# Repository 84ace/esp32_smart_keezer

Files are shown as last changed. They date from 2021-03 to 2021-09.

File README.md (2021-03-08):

<!-- PROJECT SHIELDS -->
<!--
*** I'm using markdown "reference style" links for readability.
*** Reference links are enclosed in brackets [ ] instead of parentheses ( ).
*** See the bottom of this document for the declaration of the reference variables
*** for contributors-url, forks-url, etc. This is an optional, concise syntax you may use.
*** https://www.markdownguide.org/basic-syntax/#reference-style-links
-->
[][contributors-url]
[][forks-url]
[][stars-url]
[][issues-url]
[][license-url]
[][linkedin-url]

<!-- PROJECT LOGO -->
<br />
<p align="center">
  <a href="https://github.com/84ace/esp32_smart_keezer">
    
  </a>

  <h3 align="center">ESP32 Smart Keezer</h3>

  <p align="center">
    Monitoring the beer flow!
    <br />
    <a href="https://github.com/84ace/esp32_smart_keezer/wiki"><strong>Explore the docs »</strong></a>
    <br />
    <br />
    <a href="https://github.com/84ace/esp32_smart_keezer/tree/master/board_images">Board Images</a>
    <a href="https://github.com/84ace/esp32_smart_keezer/issues">Report Bug</a>
    <a href="https://github.com/84ace/esp32_smart_keezer/issues">Request Feature</a>
  </p>
</p>

<!-- TABLE OF CONTENTS -->
<details open="open">
  <summary>Table of Contents</summary>
  <ol>
    <li>
      <a href="#about-the-project">About The Project</a>
      <ul>
        <li><a href="#main-features">Main Features</a></li>
        <li><a href="#whats-missing">What's Missing</a></li>
      </ul>
    </li>
    <li>
      <a href="#get-the-isolator">Get the Smart Keezer Gear</a>
    </li>
    <li><a href="#roadmap">Roadmap</a></li>
    <li><a href="#contributing">Contributing</a></li>
    <li><a href="#made-with">Made with</a></li>
    <li><a href="#license">License</a></li>
    <li><a href="#contact">Contact</a></li>
    <li><a href="#acknowledgements">Acknowledgements</a></li>
  </ol>
</details>

<!-- ABOUT THE PROJECT -->
## About The Project

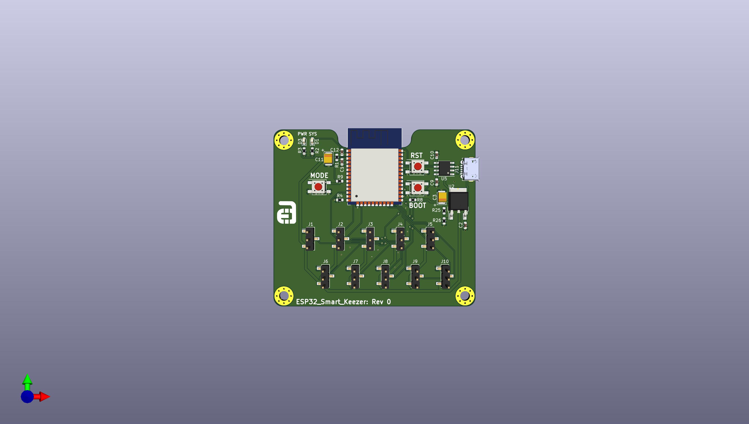
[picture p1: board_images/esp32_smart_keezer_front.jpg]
ESP32 Smart Keezer
[](https://github.com/84ace/esp32_smart_keezer/raw/master/board_images/esp32_smart_keezer_front.jpg)

The ESP32 Smart Keezer was created so that we could monitor things inside the Keezer a bit better (so we knew when we were going to run out of beer), and also so we could have a cooler way of displaying what beers were on tap.

<!-- MAIN FEATURES -->
## Main Features:
* Web based  config (webserver)
* 10 channel flow meter
* Bluetooth (to update the tap handles)
* WiFi
* USB (for power and flashing/debug)

<!-- WHAT"S MISSING -->
## What's missing:
* Many many things

If you would like to contribute an app please contact me via the <a href="https://github.com/84ace/esp32_smart_keezer/tree/master/board_images">issues</a> page.

<!-- GETTING STARTED 
## Get the hardware

There are two ways to get started: 
* You can either take the easy(er) way and buy a pre-made unit from [here](https://placeholder.com/) 
* you can send the gerber files off to your favourite fab house, order the components, assemble the board and print the enclosure yourself.

Your choice!

-->

<!-- ROADMAP -->
## Roadmap

See the [open issues](https://github.com/84ace/esp32_smart_keezer/issues) for a list of proposed features (and known issues).

<!-- CONTRIBUTING -->
## Contributing

Contributions are what make the open source community such an amazing place to be learn, inspire, and create. Any contributions you make are **greatly appreciated**.

1. Fork the Project
2. Create your Feature Branch (`git checkout -b feature/AmazingFeature`)
3. Commit your Changes (`git commit -m 'Add some AmazingFeature'`)
4. Push to the Branch (`git push origin feature/AmazingFeature`)
5. Open a Pull Request

<!-- MADE WITH -->
## Made With:
* [KiCad - Electronic Design Automation Suite](https://kicad.org/)
* [Fusion360 - CAD Software](https://www.autodesk.com.au/products/fusion-360/overview)
* [JLCPCB - PCB Fabrication Manufacturer](https://jlcpcb.com/)

<!-- LICENSE -->
## License

Distributed under the MIT License. See `LICENSE` for more information.

<!-- CONTACT -->
## Contact

84ace - [@Racea_Quigg](https://twitter.com/@RaceaQuigg)

Project Link: [https://github.com/84ace/esp32_smart_keezer](https://github.com/84ace)

<!-- MARKDOWN LINKS & IMAGES -->
<!-- https://www.markdownguide.org/basic-syntax/#reference-style-links -->
[contributors-shield]: https://img.shields.io/github/contributors/84ace/esp32_smart_keezer.svg?style=for-the-badge
[contributors-url]: https://github.com/84ace/esp32_smart_keezer/graphs/contributors
[forks-shield]: https://img.shields.io/github/forks/84ace/esp32_smart_keezer.svg?style=for-the-badge
[forks-url]: https://github.com/84ace/esp32_smart_keezer/network/members
[stars-shield]: https://img.shields.io/github/stars/84ace/esp32_smart_keezer.svg?style=for-the-badge
[stars-url]: https://github.com/84ace/esp32_smart_keezer/stargazers
[issues-shield]: https://img.shields.io/github/issues/84ace/esp32_smart_keezer.svg?style=for-the-badge
[issues-url]: https://github.com/84ace/esp32_smart_keezer/issues
[license-shield]: https://img.shields.io/github/license/84ace/esp32_smart_keezer.svg?style=for-the-badge
[license-url]: https://github.com/84ace/esp32_smart_keezer/blob/master/LICENSE.txt
[linkedin-shield]: https://img.shields.io/badge/-LinkedIn-black.svg?style=for-the-badge&logo=linkedin&colorB=555
[linkedin-url]: https://www.linkedin.com/in/acea-quigg-2007036b/
[product-screenshot]: board_images/esp32_smart_keezer_front.jpg

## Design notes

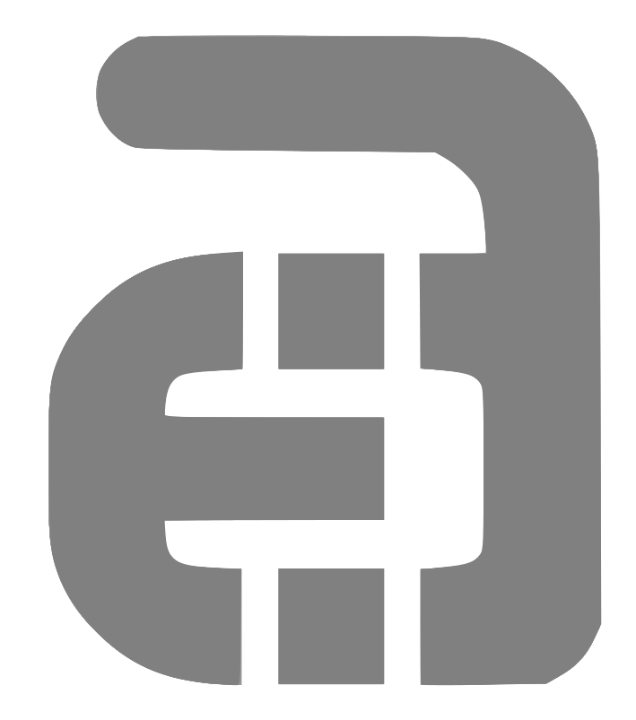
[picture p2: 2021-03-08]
images/.svg2shenzhen-cache/images/B.SilkS_g1226.png

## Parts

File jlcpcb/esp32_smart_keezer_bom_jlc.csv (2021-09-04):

Comment | Designator | Footprint | LCSC Part #
220uF | C2 | C_Elec_6.3x7.7 | C371974
220uF | C6 | CP_EIA-3528-15_AVX-H | C30242
1uF | C11 | CP_EIA-3528-21_Kemet-B | C169224
100n | C12,C1,C10,C9,C3 | C_0603_1608Metric | C14663
MAIN LED | D1 | LED_0603_1608Metric | C2286
POWER LED | D3 | LED_0603_1608Metric | C2286
SS34 | D4,D2 | D_SMA | C8678
Conn_01x03_Male | J1,J4,J5,J2,J3,J10,J8,J9,J6,J7 | PinHeader_1x03_P2.54mm_Vertical_SMD_Pin1Left | C780061
USB_B_Micro | J11 | USB_Micro_SHOU-HAN-MicroXNJ_C404969_Horizontal | C404969
Barrel_Jack_MountingPin | J12 | BarrelJack_Wuerth_6941xx301002 | C136744
47uH | L1 | L_Bourns_SRN6045TA | C36414
10k | R1,R8,R4,R9 | R_0603_1608Metric | C25804
3.6k | R2,R3 | R_0603_1608Metric | C22980
1M | R7 | R_0603_1608Metric | C22935
C492887 | SW1,SW2,SW3 | TS4550TP | C492887
ESP32-WROOM-32D | U1 | ESP32-WROOM-32 | C473012
XL1509_SOP8 | U2 | SOIC-8_3.9x4.9mm_P1.27mm | C2681226
CH340N | U5 | SOIC-8_3.9x4.9mm_P1.27mm | C506813

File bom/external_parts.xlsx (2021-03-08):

$8.82 | 3.3V 1/2" Stainless 1-30LPM | https://www.aliexpress.com/item/32834744712.html
 | 3.3V 3/4" Aluminium 1-30LPM | https://www.aliexpress.com/item/32883880511.html

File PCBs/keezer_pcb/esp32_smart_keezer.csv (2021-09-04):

Id | Designator | Package | Quantity | Designation | Supplier and ref
1 | Ref** | aces_electronics_small_front | 1 | Val**
2 | J11 | USB_Micro_SHOU-HAN-MicroXNJ_C404969_Horizontal | 1 | USB_B_Micro
3 | H1,H1,H1,H1 | MountingHole_3.2mm_M3_Pad_Via | 4 | MountingHole_3.2mm_M3_Pad_Via
4 | C1,C9,C10,C12,C3 | C_0603_1608Metric | 5 | 100n
5 | C11 | CP_EIA-3528-21_Kemet-B | 1 | 1uF
6 | D1 | LED_0603_1608Metric | 1 | MAIN LED
7 | D3 | LED_0603_1608Metric | 1 | POWER LED
8 | R1,R4,R8,R9 | R_0603_1608Metric | 4 | 10k
9 | R2,R3 | R_0603_1608Metric | 2 | 3.6k
10 | U1 | ESP32-WROOM-32 | 1 | ESP32-WROOM-32D
11 | SW1,SW2,SW3 | TS4550TP | 3 | C492887
12 | U5 | SOIC-8_3.9x4.9mm_P1.27mm | 1 | CH340N
13 | J1,J2,J3,J4,J5,J6,J7,J8,J9,J10 | PinHeader_1x03_P2.54mm_Vertical_SMD_Pin1Left | 10 | Conn_01x03_Male
14 | D4,D2 | D_SMA | 2 | SS34
15 | J12 | BarrelJack_Wuerth_6941xx301002 | 1 | Barrel_Jack_MountingPin
16 | C2 | C_Elec_6.3x7.7 | 1 | 220uF
17 | C6 | CP_EIA-3528-15_AVX-H | 1 | 220uF
18 | L1 | L_Bourns_SRN6045TA | 1 | 47uH
19 | R7 | R_0603_1608Metric | 1 | 1M
20 | U2 | SOIC-8_3.9x4.9mm_P1.27mm | 1 | XL1509_SOP8

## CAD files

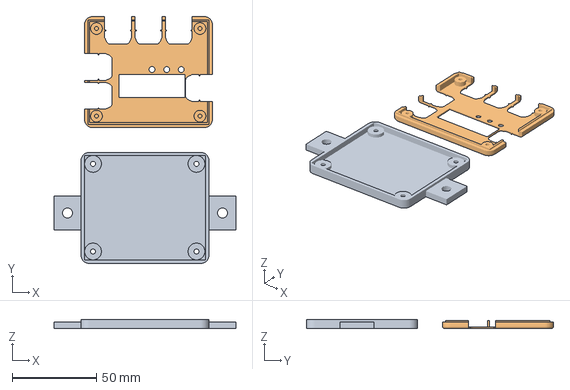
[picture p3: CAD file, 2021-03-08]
enclosure/REV_A.3mf
108.0 x 146.6 x 5.60 mm
e16b49ae-1aed-4ee6-b51c-7ca3a6dbe336.stl
ccecfdcf-7b8e-40b3-9f25-145435015e84.stl

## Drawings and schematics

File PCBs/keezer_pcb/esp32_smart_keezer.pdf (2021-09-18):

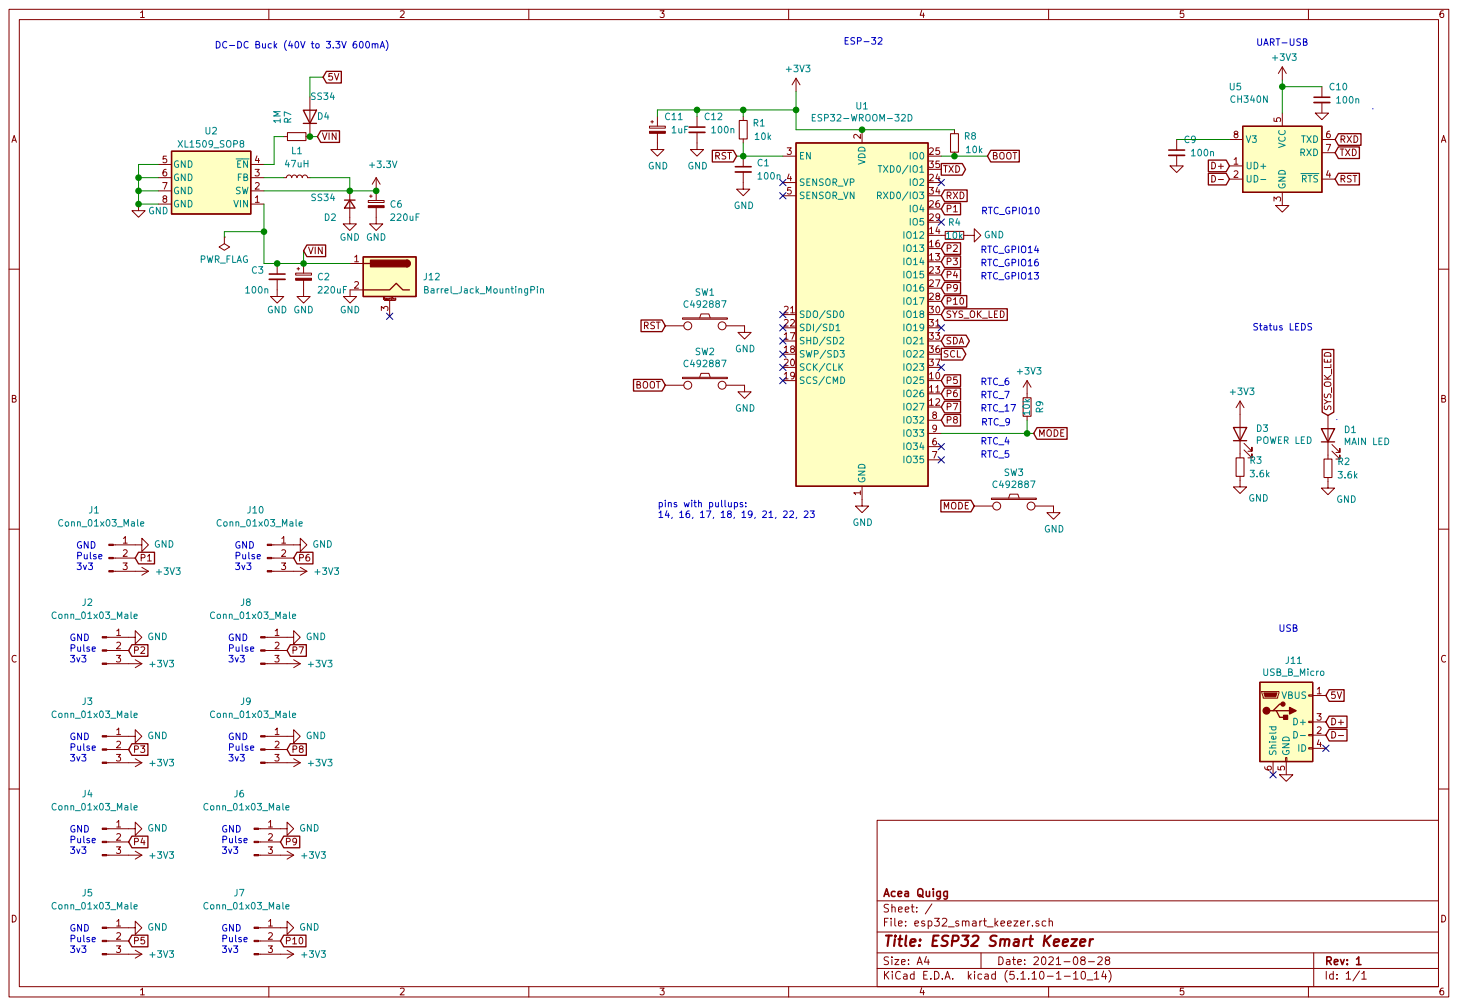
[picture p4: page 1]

File: esp32_smart_keezer.sch Sheet: / Acea Quigg

Id: 1/1 Title: ESP32 Smart Keezer

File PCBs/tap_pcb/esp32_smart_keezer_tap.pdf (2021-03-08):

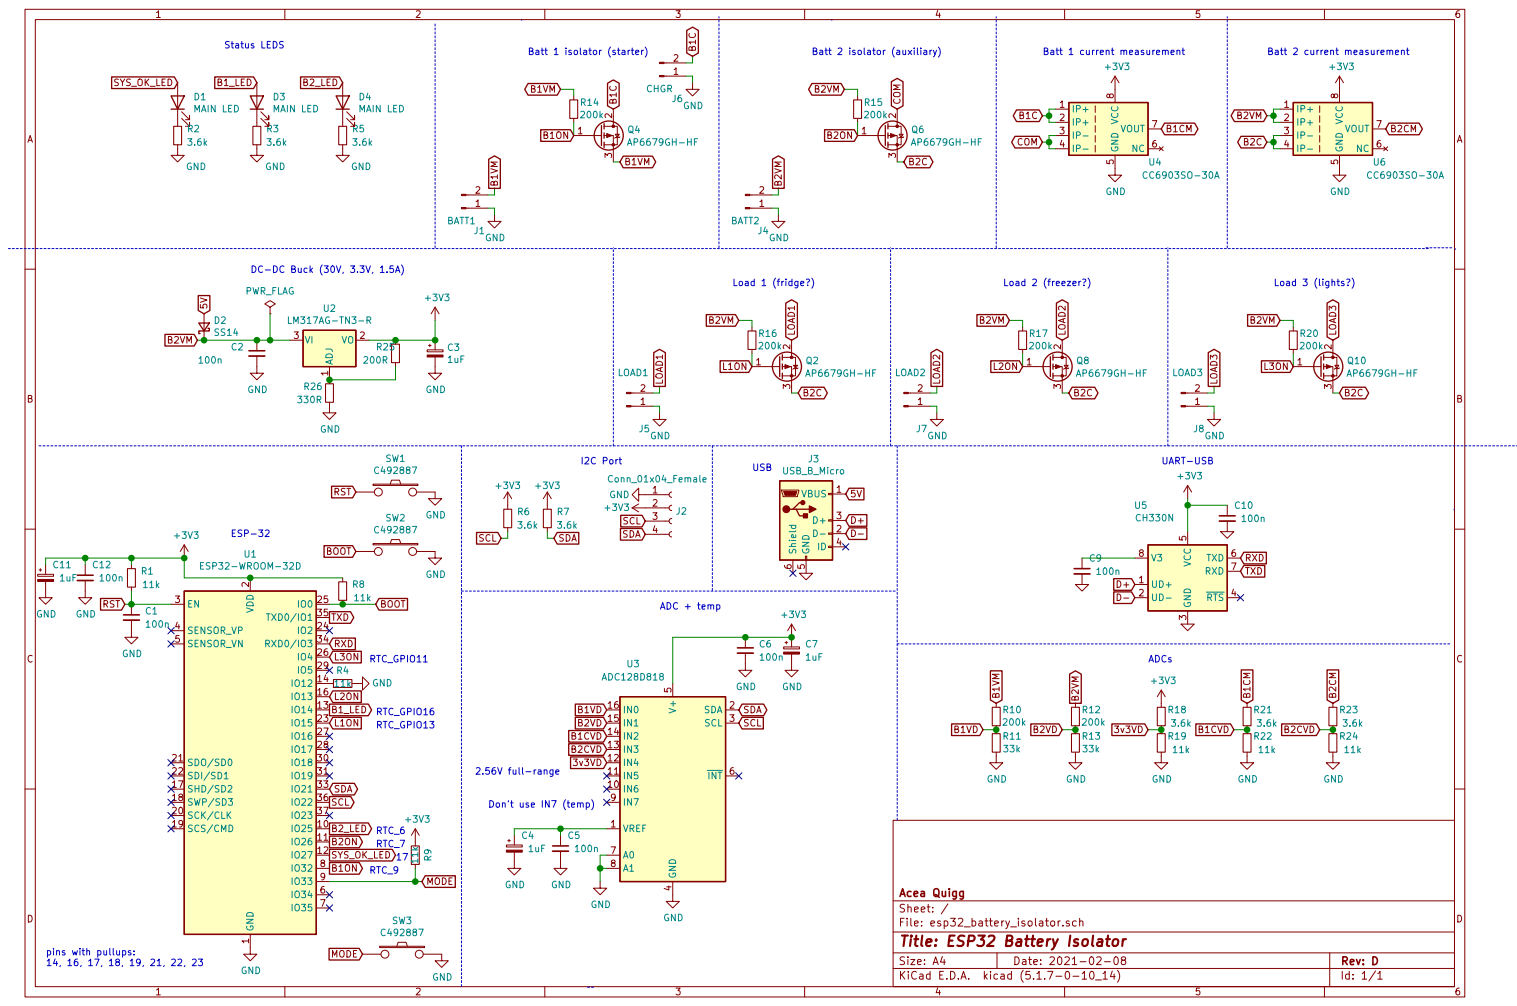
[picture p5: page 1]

Batt 2 isolator (auxiliary) Status LEDS

Load 3 (lights?) UART-USB

2 SCK/CLK 20 SDO/SD0 21 SDI/SD1 22

File: esp32_battery_isolator.sch Sheet: / Acea Quigg GND GND

Id: 1/1 Title: ESP32 Battery Isolator

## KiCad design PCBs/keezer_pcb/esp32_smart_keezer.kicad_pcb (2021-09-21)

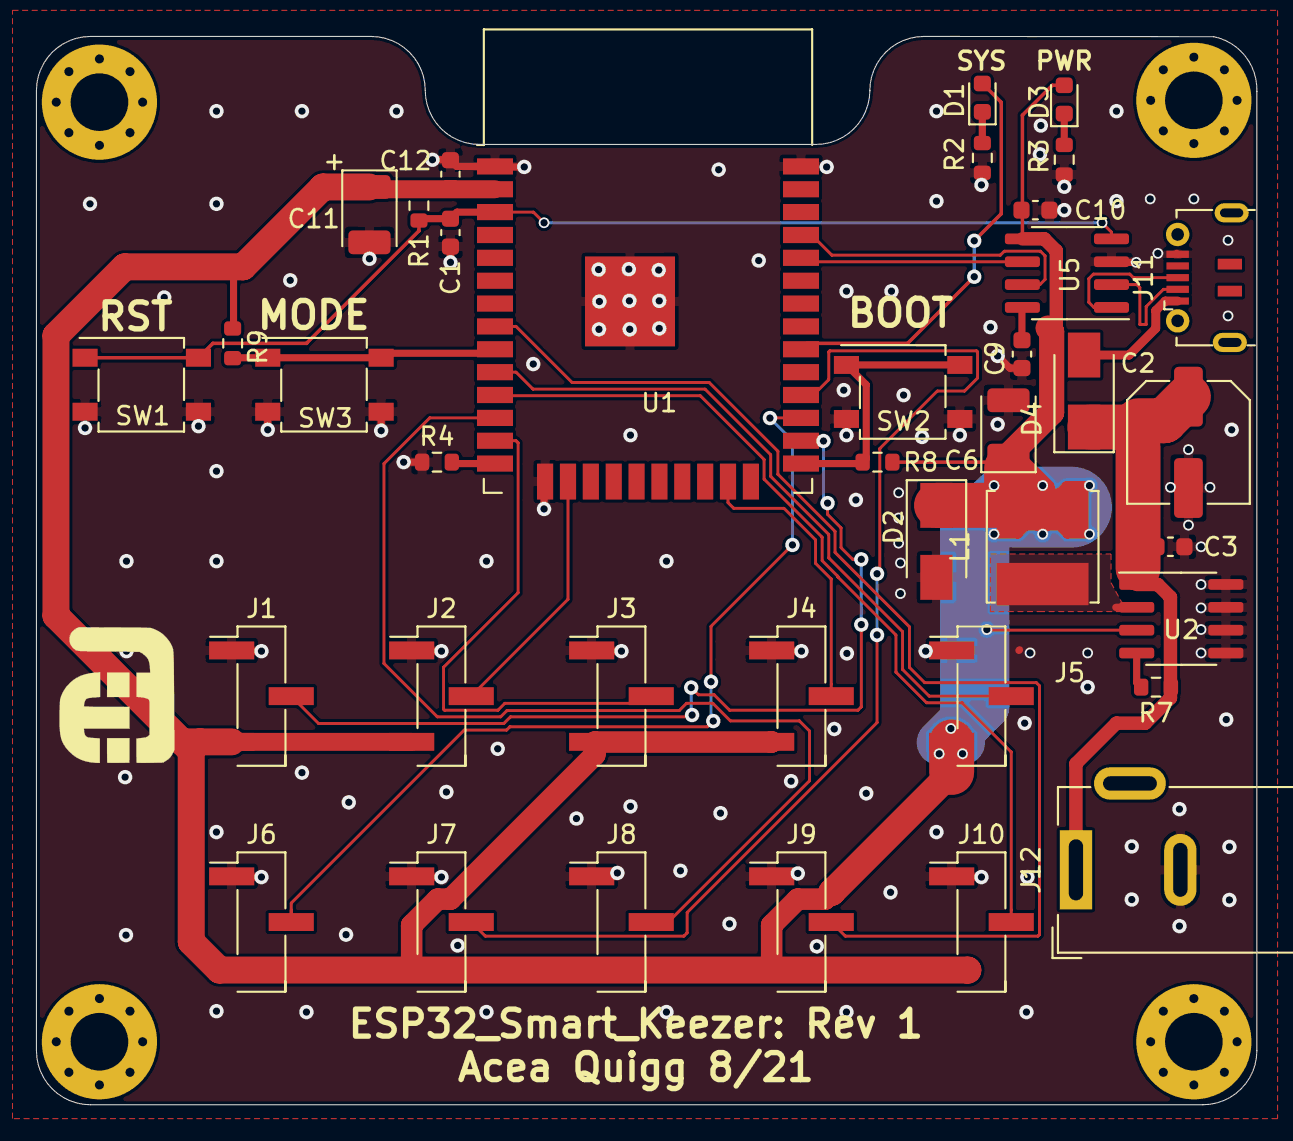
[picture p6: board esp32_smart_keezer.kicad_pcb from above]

Board: 2 copper layers, 67.8 x 59.3 mm, 43 parts (0 on the bottom side), 28 nets.

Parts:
C1, C3, C9, C10, C12: 100n; C_0603_1608Metric
C2: 220uF; C_Elec_6.3x7.7
C6: 220uF; CP_EIA-3528-15_AVX-H
C11: 1uF; CP_EIA-3528-21_Kemet-B
D1: MAIN LED; LED_0603_1608Metric
D2, D4: SS34; D_SMA
D3: POWER LED; LED_0603_1608Metric
H1, H1#2, H1#3, H1#4: MountingHole_3.2mm_M3_Pad_Via
J1, J2, J3, J4, J5, J6, J7, J8, J9, J10: Conn_01x03_Male; PinHeader_1x03_P2.54mm_Vertical_SMD_Pin1Left
J11: USB_B_Micro; USB_Micro_SHOU-HAN-MicroXNJ_C404969_Horizontal
J12: Barrel_Jack_MountingPin; BarrelJack_Wuerth_6941xx301002
L1: 47uH; L_Bourns_SRN6045TA
R1, R4, R8, R9: 10k; R_0603_1608Metric
R2, R3: 3.6k; R_0603_1608Metric
R7: 1M; R_0603_1608Metric
Ref**: Val**; aces_electronics_small_front
SW1, SW2, SW3: C492887; TS4550TP
U1: ESP32-WROOM-32D; ESP32-WROOM-32
U2: XL1509_SOP8; SOIC-8_3.9x4.9mm_P1.27mm
U5: CH340N; SOIC-8_3.9x4.9mm_P1.27mm

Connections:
5V: D4.2, J11.1
+3V3: C6.1, C10.1, C11.1, C12.1, D2.1, D3.2, J1.3, J2.3, J3.3, J4.3, J5.3, J6.3, J7.3, J8.3, J9.3, J10.3, L1.2, R1.1, R8.1, R9.2, U1.2, U2.3, U5.5
BOOT: R8.2, SW2.1, U1.25
D+: J11.3, U5.1
D-: J11.2, U5.2
GND: C1.2, C2.2, C3.2, C6.2, C9.2, C10.2, C11.2, C12.2, D2.2, J1.1, J2.1, J3.1, J4.1, J5.1, J6.1, J7.1, J8.1, J9.1, J10.1, J11.5, J12.2, R2.2, R3.2, R4.1, SW1.2, SW2.2, SW3.2, U1.1, U1.15, U1.38, U1.39, U2.5, U2.6, U2.7, U2.8, U5.3
MODE: R9.1, SW3.1, U1.9
unnamed: C9.1, U5.8
unnamed: D1.1, R2.1
unnamed: D3.1, R3.1
unnamed: L1.1, U2.2
unnamed: R4.2, U1.14
unnamed: R7.2, U2.4
P1: J1.2, U1.26
P2: J2.2, U1.16
P3: J3.2, U1.13
P4: J4.2, U1.23
P5: J5.2, U1.10
P6: J10.2, U1.11
P7: J8.2, U1.12
P8: J9.2, U1.8
P9: J6.2, U1.27
P10: J7.2, U1.28
RST: C1.1, R1.2, SW1.1, U1.3, U5.4
RXD: U1.34, U5.6
SYS_OK_LED: D1.2, U1.30
TXD: U1.35, U5.7
VIN: C2.1, C3.1, D4.1, J12.1, R7.1, U2.1

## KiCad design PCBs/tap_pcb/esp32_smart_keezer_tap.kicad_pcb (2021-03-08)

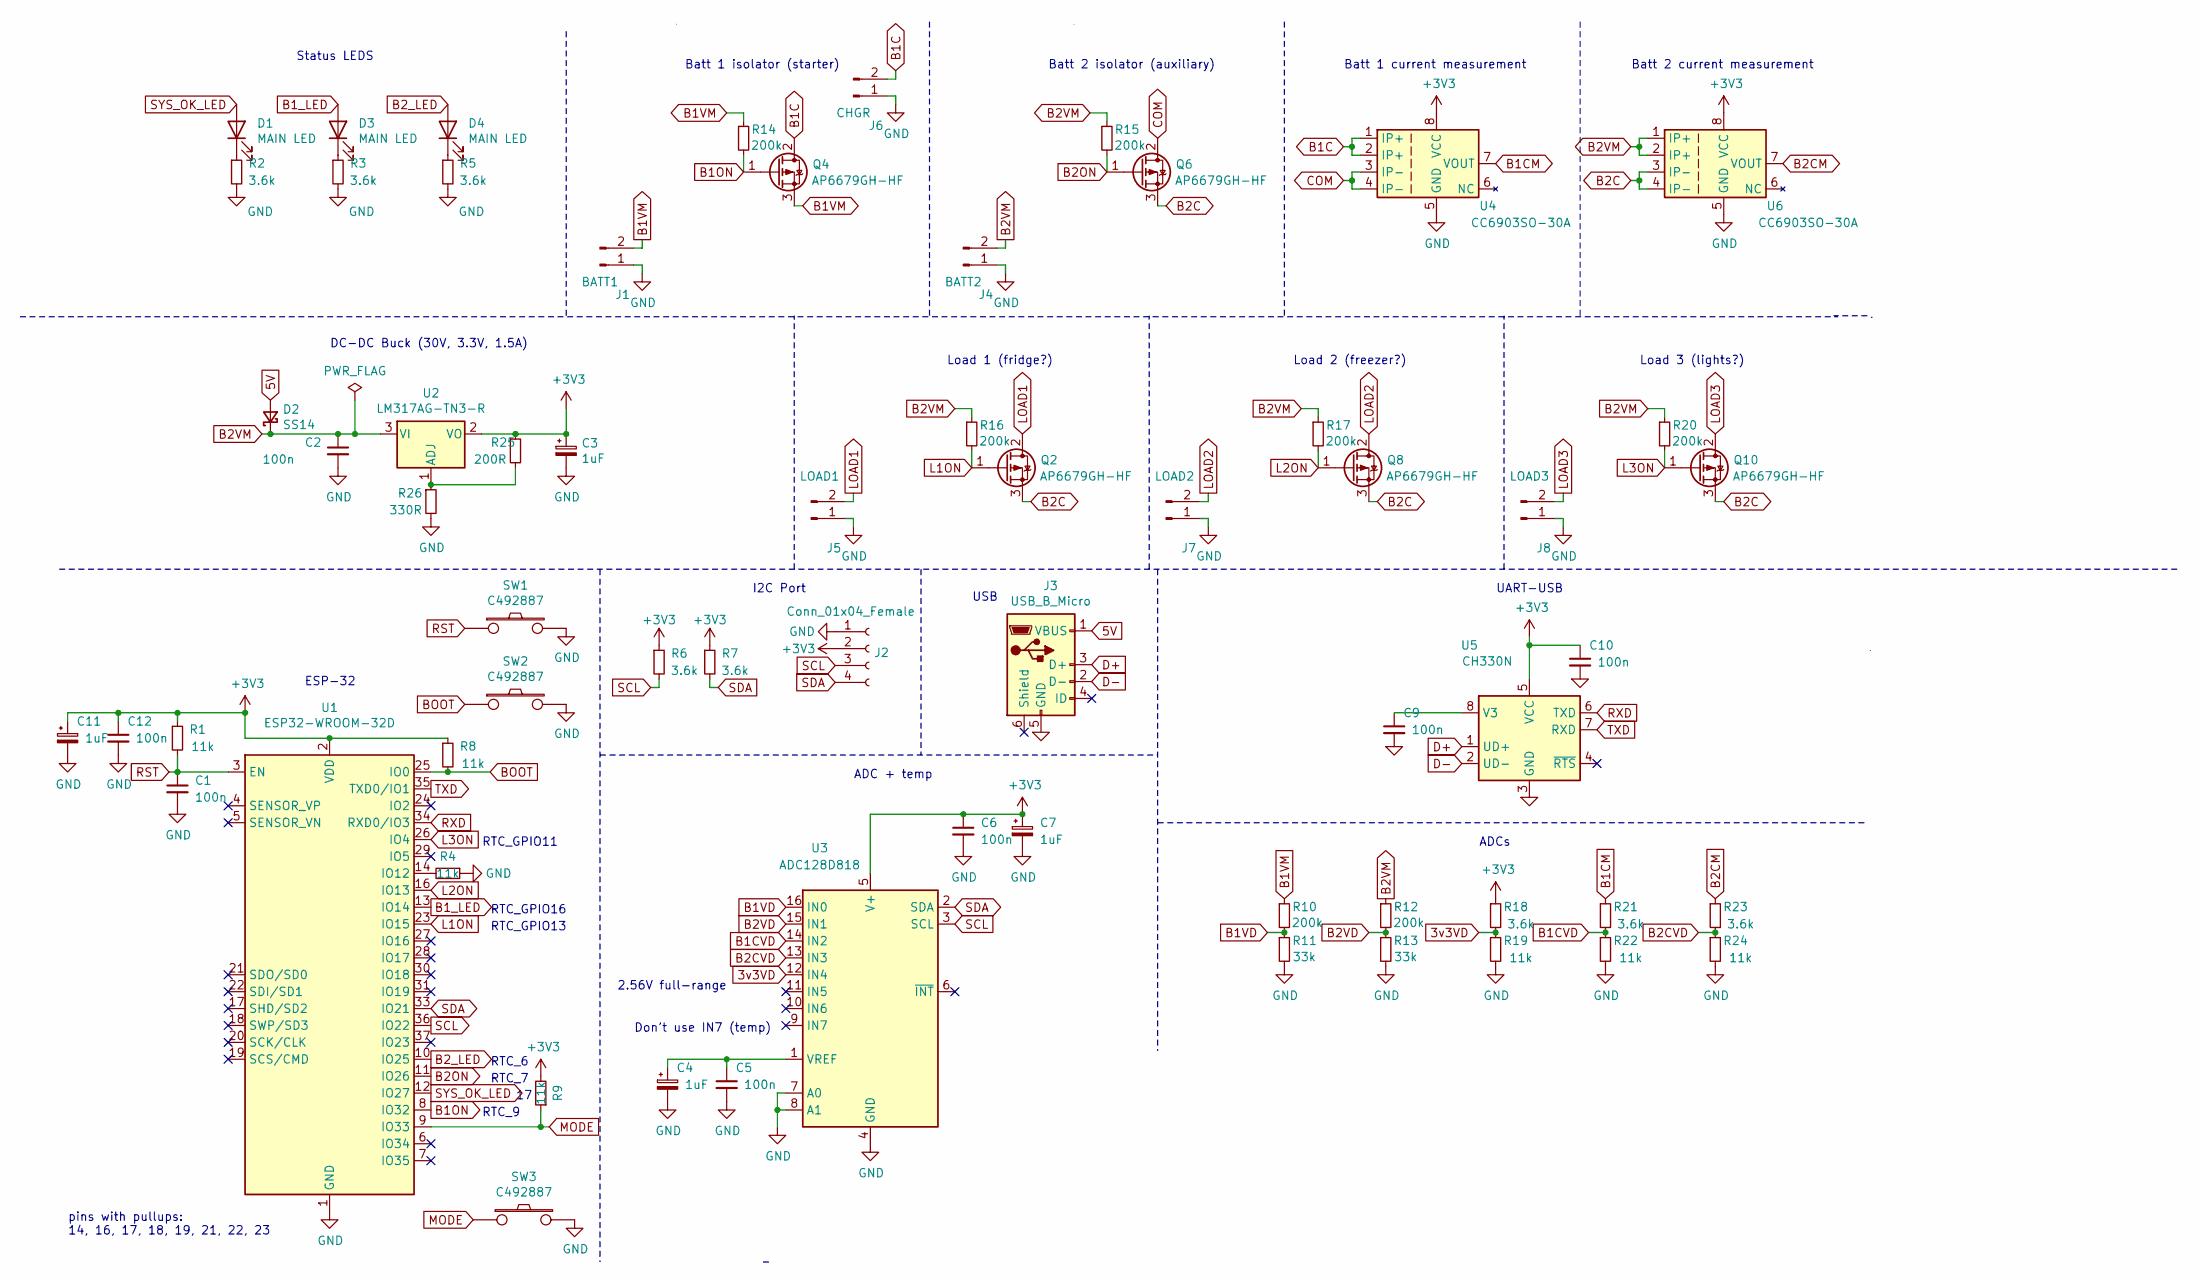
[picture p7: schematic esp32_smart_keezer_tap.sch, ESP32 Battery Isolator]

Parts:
C1, C2, C5, C6, C9, C10, C12: 100n; C_0603_1608Metric; lcsc_part_number C14663
C3, C4, C7, C11: 1uF; CP_EIA-3528-21_Kemet-B; lcsc_part_number C169224
D1, D3, D4: MAIN LED; LED_0603_1608Metric; lcsc_part_number C2286
D2: SS14; D_SMA; mfr_part_number SS14; lcsc_part_number C2480
J1: BATT1; AMASS_XT60PW-M; lcsc_part_number C98732
J2: Conn_01x04_Female; PinSocket_1x04_P2.54mm_Vertical
J3: USB_B_Micro; USB_Micro_SHOU-HAN-MicroXNJ_C404969_Horizontal; lcsc_part_number C404969
J4: BATT2; AMASS_XT60PW-M; lcsc_part_number C98732
J5: LOAD1; AMASS_XT60PW-F; lcsc_part_number C428722
J6: CHGR; AMASS_XT60PW-M; lcsc_part_number C98732
J7: LOAD2; AMASS_XT60PW-F; lcsc_part_number C428722
J8: LOAD3; AMASS_XT60PW-F; lcsc_part_number C428722
Q2, Q4, Q6, Q8, Q10: AP6679GH-HF; TO-252-2; lcsc_part_number C124530
R1, R4, R8, R9, R19, R22, R24: 11k; R_0603_1608Metric; lcsc_part_number C25950
R2, R3, R5, R6, R7, R18, R21, R23: 3.6k; R_0603_1608Metric; lcsc_part_number C22980
R10, R12, R14, R15, R16, R17, R20: 200k; R_0603_1608Metric; lcsc_part_number C25811
R11, R13: 33k; R_0603_1608Metric; lcsc_part_number C4216
R25: 200R; R_0603_1608Metric; lcsc_part_number C8218
R26: 330R; R_0603_1608Metric; lcsc_part_number C23138
SW1, SW2, SW3: C492887; TS4550TP; mfr_part_number TS-1091S-A5B3-C1D2; lcsc_part_number C492887
U1: ESP32-WROOM-32D; ESP32-WROOM-32; mfr_part_number ESP32-WROOM-32D; lcsc_part_number C473012
U2: LM317AG-TN3-R; TO-252-2; lcsc_part_number C75510
U3: ADC128D818; TSSOP-16_4.4x5mm_P0.65mm; mfr_part_number ADC128D818CIMTX; lcsc_part_number C139062
U4, U6: CC6903SO-30A; SOP-8_3.9x4.9mm_P1.27mm; mfr_part_number CC6903SO-30A; lcsc_part_number C469388
U5: CH330N; SOIC-8_3.9x4.9mm_P1.27mm; mfr_part_number CH330N; lcsc_part_number C108996

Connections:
3v3VD: R18.2, R19.1, U3.12 (IN4)
5V: D2.2 (A), J3.1 (VBUS)
+3V3: C3.1, C6.1, C7.1, C10.1, C11.1, C12.1, J2.2, R1.1, R6.1, R7.1, R8.1, R9.2, R18.1, R25.1, U1.2 (VDD), U2.2 (VO), U3.5 (V+), U4.8 (VCC), U5.5 (VCC), U6.8 (VCC)
B1C: J6.2, Q4.2 (D), U4.1 (IP+), U4.2 (IP+)
B1CM: R21.1, U4.7 (VOUT)
B1CVD: R21.2, R22.1, U3.14 (IN2)
B1ON: Q4.1 (G), R14.2, U1.8 (IO32)
B1VD: R10.2, R11.1, U3.16 (IN0)
B1VM: J1.2, Q4.3 (S), R10.1, R14.1
B1_LED: D3.2 (A), U1.13 (IO14)
B2C: Q2.3 (S), Q6.3 (S), Q8.3 (S), Q10.3 (S), U6.3 (IP-), U6.4 (IP-)
B2CM: R23.1, U6.7 (VOUT)
B2CVD: R23.2, R24.1, U3.13 (IN3)
B2ON: Q6.1 (G), R15.2, U1.11 (IO26)
B2VD: R12.2, R13.1, U3.15 (IN1)
B2VM: C2.1, D2.1 (K), J4.2, R12.1, R15.1, R16.1, R17.1, R20.1, U2.3 (VI), U6.1 (IP+), U6.2 (IP+)
B2_LED: D4.2 (A), U1.10 (IO25)
BOOT: R8.2, SW2.1, U1.25 (IO0)
COM: Q6.2 (D), U4.3 (IP-), U4.4 (IP-)
D+: J3.3 (D+), U5.1 (UD+)
D-: J3.2 (D-), U5.2 (UD-)
GND: C1.2, C2.2, C3.2, C4.2, C5.2, C6.2, C7.2, C9.2, C10.2, C11.2, C12.2, J1.1, J2.1, J3.5 (GND), J4.1, J5.1, J6.1, J7.1, J8.1, R2.2, R3.2, R4.1, R5.2, R11.2, R13.2, R19.2, R22.2, R24.2, R26.2, SW1.2, SW2.2, SW3.2, U1.1 (GND), U1.15 (GND), U1.38 (GND), U1.39 (GND), U3.4 (GND), U3.7 (A0), U3.8 (A1), U4.5 (GND), U5.3 (GND), U6.5 (GND)
L1ON: Q2.1 (G), R16.2, U1.23 (IO15)
L2ON: Q8.1 (G), R17.2, U1.16 (IO13)
L3ON: Q10.1 (G), R20.2, U1.26 (IO4)
LOAD1: J5.2, Q2.2 (D)
LOAD2: J7.2, Q8.2 (D)
LOAD3: J8.2, Q10.2 (D)
MODE: R9.1, SW3.1, U1.9 (IO33)
unnamed: C4.1, C5.1, U3.1 (VREF)
unnamed: C9.1, U5.8 (V3)
unnamed: D1.1 (K), R2.1
unnamed: D3.1 (K), R3.1
unnamed: D4.1 (K), R5.1
unnamed: R4.2, U1.14 (IO12)
unnamed: R25.2, R26.1, U2.1 (ADJ)
RST: C1.1, R1.2, SW1.1, U1.3 (EN)
RXD: U1.34 (RXD0/IO3), U5.6 (TXD)
SCL: J2.3, R6.2, U1.36 (IO22), U3.3 (SCL)
SDA: J2.4, R7.2, U1.33 (IO21), U3.2 (SDA)
SYS_OK_LED: D1.2 (A), U1.12 (IO27)
TXD: U1.35 (TXD0/IO1), U5.7 (RXD)

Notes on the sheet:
Status LEDS
ESP-32
ADCs
I2C Port
DC-DC Buck (30V, 3.3V, 1.5A)
2.56V full-range
ADC + temp
USB
UART-USB
Batt 1 isolator (starter)
Batt 2 current measurement
Don’t use IN7 (temp)
Batt 1 current measurement
Load 1 (fridge?)
Load 2 (freezer?)
Load 3 (lights?)
Batt 2 isolator (auxiliary)
pins with pullups: 14, 16, 17, 18, 19, 21, 22, 23
RTC_GPIO11
RTC_GPIO16
RTC_6
RTC_9
RTC_GPIO13
RTC_7

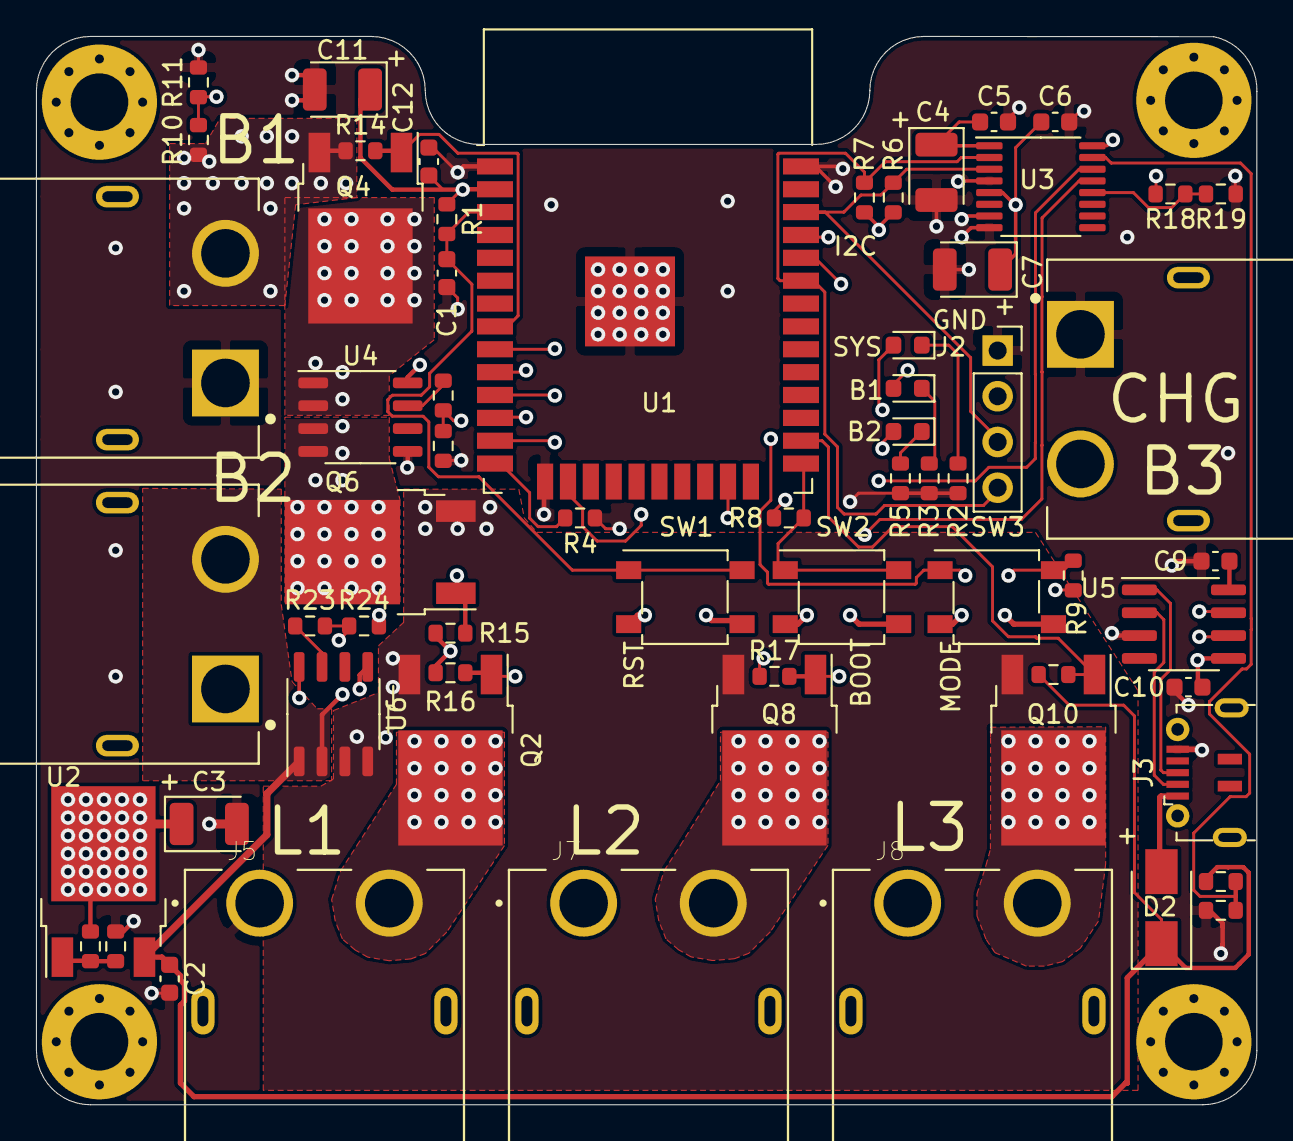
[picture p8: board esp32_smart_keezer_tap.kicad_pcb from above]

Board: 4 copper layers, 67.8 x 59.3 mm, 67 parts (0 on the bottom side), 42 nets.

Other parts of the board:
H1, H1#2, H1#3, H1#4: MountingHole_3.2mm_M3_Pad_Via

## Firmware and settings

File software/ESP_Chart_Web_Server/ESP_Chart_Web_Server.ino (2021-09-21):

// Import required libraries

#include <WiFi.h>
#include <ESPAsyncWebServer.h>
#include <SPIFFS.h>
#include <AsyncElegantOTA.h>
#include <Wire.h>
#include <Adafruit_Sensor.h>
#include <Adafruit_BME280.h>
#include <Preferences.h>
#include <SimpleTimer.h>

#define REV1 // PCB REV 1

#ifdef REV1
#define LED_BUILTIN 18
#define SENSOR1 4   // beer1 (J1)
#define SENSOR2 13  // beer2 (J2)
#define SENSOR3 14  // beer3 (J3)
#define SENSOR4 15  // beer4 (J4)
#define SENSOR5 25  // beer5 (J5)
#define SENSOR6 16  // beer6 (J6)
#define SENSOR7 17  // beer7 (J7)
#define SENSOR8 27  // beer8 (J8)
#define SENSOR9 32  // beer9 (J9)
#define SENSOR10 26 // beer10 (J10)
#endif

// LED stuff
int ledState = HIGH;
int stopLED = 1;
unsigned long previousMillisLED = 0;
long blinkInterval = 1000;

// ToDo: use STA_AP mode to allow initial setup over WiFi - done 18/09/21
// ToDo: create OTA upload page for .bin firmware updates - done 18/09/21
// ToDo: create OTA upload page for SPIFFS partition updates - done 18/09/21
// ToDo: create beer volume set from in settings - done 18/09/21
// ToDo: add a flow calibration/modifier in settings - done 20/09/21
// ToDo: save beer names from settings to flash so they are persitent - done 19/09/21
// ToDo: save beer volumes from settings to flash so they are persitent - done 19/09/21
// ToDo: save beer volumes from flow readings to flash so they are persitent - done 20/09/21
// ToDo: validate beer volumes and name input field data - done 19/09/21
// ToDo: configure consumption chart to dynamically update names and volumes - done 21/09/21
// ToDo: configure overview to dynamically update beer names and volumes - volumes done 21/09/21
// ToDo: add an fast LED blink to indicate there is an error (wifi not connected etc) - done 20/09/21
// ToDo: add visual feedback that form submitted correctly - done 20/09/21
// ToDo: consumption charts need to honour beer count and render the right amount of charts
// ToDo: implement a mode press button to wipe WiFi creds and trigger WiFi AP for setup
// ToDo: sync data colours between charts - done 21/09/21
// ToDo: create a way to backup and restore beer data before a firmware upgrade - done (not needed) 19/09/21
// ToDo: test/build CSS HTML layouts for different sized screens/mobile < this probably won't happen ;)
// ToDo: write some tests...

// Replace with your network credentials
Preferences preferences;

String pwifiSSID;
String pwifiPassword;

const char *wifiSSID = "ShelveNET";
const char *wifiPassword = "buttpiratry";

int wifiDisconnected = 0;

void (*resetFunc)(void) = 0; // declare reset fuction at address 0

const char *PARAM_INPUT_0 = "numberofbeers";
const char *PARAM_INPUT_1 = "beer1name";
const char *PARAM_INPUT_2 = "beer2name";
const char *PARAM_INPUT_3 = "beer3name";
const char *PARAM_INPUT_4 = "beer4name";
const char *PARAM_INPUT_5 = "beer5name";
const char *PARAM_INPUT_6 = "beer6name";
const char *PARAM_INPUT_7 = "beer7name";
const char *PARAM_INPUT_8 = "beer8name";
const char *PARAM_INPUT_9 = "beer9name";
const char *PARAM_INPUT_10 = "beer10name";
const char *PARAM_INPUT_11 = "beer1volume";
const char *PARAM_INPUT_12 = "beer2volume";
const char *PARAM_INPUT_13 = "beer3volume";
const char *PARAM_INPUT_14 = "beer4volume";
const char *PARAM_INPUT_15 = "beer5volume";
const char *PARAM_INPUT_16 = "beer6volume";
const char *PARAM_INPUT_17 = "beer7volume";
const char *PARAM_INPUT_18 = "beer8volume";
const char *PARAM_INPUT_19 = "beer9volume";
const char *PARAM_INPUT_20 = "beer10volume";
const char *PARAM_INPUT_21 = "wifissid";
const char *PARAM_INPUT_22 = "wifipassword";
const char *PARAM_INPUT_23 = "reset";
const char *PARAM_INPUT_24 = "flowmultiplier";
const char *PARAM_INPUT_25 = "allbeernames";
const char *PARAM_INPUT_26 = "overviewchartname";

String beer1Name;
String beer2Name;
String beer3Name;
String beer4Name;
String beer5Name;
String beer6Name;
String beer7Name;
String beer8Name;
String beer9Name;
String beer10Name;
String overviewChartName;
String statsString = "";
String beerNameString = "";
String jsonBeerNamesString ="";

int numberOfBeers = 10;
float beer1Volume;
float beer2Volume;
float beer3Volume;
float beer4Volume;
float beer5Volume;
float beer6Volume;
float beer7Volume;
float beer8Volume;
float beer9Volume;
float beer10Volume;
float tempBeer1Volume;
float tempBeer2Volume;
float tempBeer3Volume;
float tempBeer4Volume;
float tempBeer5Volume;
float tempBeer6Volume;
float tempBeer7Volume;
float tempBeer8Volume;
float tempBeer9Volume;
float tempBeer10Volume;
float calibrationFactor = 98;

bool status;
char promBytes[32];

int pulse1 = 0;
long currentMillis1 = 0;
long previousMillis1 = 0;
int flowMilliLitres1;
int totalMilliLitres1;
byte pulseSec1 = 0;
volatile byte pulseCount1;
float beer1Litres = 0;
char beer1LitresChar[6] = "";
float flowRate1;

void IRAM_ATTR pulseCount1er()
{
  pulseCount1++;
}

int pulse2 = 0;
long currentMillis2 = 0;
long previousMillis2 = 0;
int flowMilliLitres2;
int totalMilliLitres2;
byte pulseSec2 = 0;
volatile byte pulseCount2;
float beer2Litres = 0;
char beer2LitresChar[6] = "";
float flowRate2;

void IRAM_ATTR pulseCount2er()
{
  pulseCount2++;
}

int pulse3 = 0;
long currentMillis3 = 0;
long previousMillis3 = 0;
int flowMilliLitres3;
int totalMilliLitres3;
byte pulseSec3 = 0;
volatile byte pulseCount3;
float beer3Litres = 0;
char beer3LitresChar[6] = "";
float flowRate3;

void IRAM_ATTR pulseCount3er()
{
  pulseCount3++;
}

int pulse4 = 0;
long currentMillis4 = 0;
long previousMillis4 = 0;
int flowMilliLitres4;
int totalMilliLitres4;
byte pulseSec4 = 0;
volatile byte pulseCount4;
float beer4Litres = 0;
char beer4LitresChar[6] = "";
float flowRate4;

void IRAM_ATTR pulseCount4er()
{
  pulseCount4++;
}

int pulse5 = 0;
long currentMillis5 = 0;
long previousMillis5 = 0;
int flowMilliLitres5;
int totalMilliLitres5;
byte pulseSec5 = 0;
volatile byte pulseCount5;
float beer5Litres = 0;
char beer5LitresChar[6] = "";
float flowRate5;

void IRAM_ATTR pulseCount5er()
{
  pulseCount5++;
}

int pulse6 = 0;
long currentMillis6 = 0;
long previousMillis6 = 0;
int flowMilliLitres6;
int totalMilliLitres6;
byte pulseSec6 = 0;
volatile byte pulseCount6;
float beer6Litres = 0;
char beer6LitresChar[6] = "";
float flowRate6;

void IRAM_ATTR pulseCount6er()
{
  pulseCount6++;
}

int pulse7 = 0;
long currentMillis7 = 0;
long previousMillis7 = 0;
int flowMilliLitres7;
int totalMilliLitres7;
byte pulseSec7 = 0;
volatile byte pulseCount7;
float beer7Litres = 0;
char beer7LitresChar[6] = "";
float flowRate7;

void IRAM_ATTR pulseCount7er()
{
  pulseCount7++;
}

int pulse8 = 0;
long currentMillis8 = 0;
long previousMillis8 = 0;
int flowMilliLitres8;
int totalMilliLitres8;
byte pulseSec8 = 0;
volatile byte pulseCount8;
float beer8Litres = 0;
char beer8LitresChar[6] = "";
float flowRate8;

void IRAM_ATTR pulseCount8er()
{
  pulseCount8++;
}

int pulse9 = 0;
long currentMillis9 = 0;
long previousMillis9 = 0;
int flowMilliLitres9;
int totalMilliLitres9;
byte pulseSec9 = 0;
volatile byte pulseCount9;
float beer9Litres = 0;
char beer9LitresChar[6] = "";
float flowRate9;

void IRAM_ATTR pulseCount9er()
{
  pulseCount9++;
}

int pulse10 = 0;
long currentMillis10 = 0;
long previousMillis10 = 0;
int flowMilliLitres10;
int totalMilliLitres10;
byte pulseSec10 = 0;
volatile byte pulseCount10;
float beer10Litres = 0;
char beer10LitresChar[6] = "";
float flowRate10;

void IRAM_ATTR pulseCount10er()
{
  pulseCount10++;
}

SimpleTimer timer;

int interval = 1000; // wait time before comparing flow data

float stats[10] = {20.00, 18.00, 16.00, 14.00, 12.00, 10.00, 8.00, 6.00, 4.00, 0.00};


// Create AsyncWebServer object on port 80
AsyncWebServer server(80);
AsyncWebSocket ws("/ws");

void onEvent(AsyncWebSocket *server, AsyncWebSocketClient *client, AwsEventType type,
             void *arg, uint8_t *data, size_t len)
{
  switch (type)
  {
  case WS_EVT_CONNECT:
    Serial.printf("WebSocket client #%u connected from %s\n", client->id(), client->remoteIP().toString().c_str());
    break;
  case WS_EVT_DISCONNECT:
    Serial.printf("WebSocket client #%u disconnected\n", client->id());
    break;
  case WS_EVT_PONG:
  case WS_EVT_ERROR:
    break;
  }
}

void initWebSocket()
{
  ws.onEvent(onEvent);
  server.addHandler(&ws);
}

void notFound(AsyncWebServerRequest *request)
{
  request->send(404, "text/plain", "Not found");
}

void setupFlowData()
{
  pinMode(SENSOR1, INPUT_PULLUP);
  pinMode(SENSOR2, INPUT_PULLUP);
  pinMode(SENSOR3, INPUT_PULLUP);
  pinMode(SENSOR4, INPUT_PULLUP);
  pinMode(SENSOR5, INPUT_PULLUP);
  pinMode(SENSOR6, INPUT_PULLUP);
  pinMode(SENSOR7, INPUT_PULLUP);
  pinMode(SENSOR8, INPUT_PULLUP);
  pinMode(SENSOR9, INPUT_PULLUP);
  pinMode(SENSOR10, INPUT_PULLUP);

  pulseCount1 = 0;
  flowRate1 = 0.0;
  flowMilliLitres1 = 0;
  totalMilliLitres1 = 0;
  previousMillis1 = 0;

  pulseCount2 = 0;
  flowRate2 = 0.0;
  flowMilliLitres2 = 0;
  totalMilliLitres2 = 0;
  previousMillis2 = 0;

  pulseCount3 = 0;
  flowRate3 = 0.0;
  flowMilliLitres3 = 0;
  totalMilliLitres3 = 0;
  previousMillis3 = 0;

  pulseCount4 = 0;
  flowRate4 = 0.0;
  flowMilliLitres4 = 0;
  totalMilliLitres4 = 0;
  previousMillis4 = 0;

  pulseCount5 = 0;
  flowRate5 = 0.0;
  flowMilliLitres5 = 0;
  totalMilliLitres5 = 0;
  previousMillis5 = 0;

  pulseCount6 = 0;
  flowRate6 = 0.0;
  flowMilliLitres6 = 0;
  totalMilliLitres6 = 0;
  previousMillis6 = 0;

  pulseCount7 = 0;
  flowRate7 = 0.0;
  flowMilliLitres7 = 0;
  totalMilliLitres7 = 0;
  previousMillis7 = 0;

  pulseCount8 = 0;
  flowRate8 = 0.0;
  flowMilliLitres8 = 0;
  totalMilliLitres8 = 0;
  previousMillis8 = 0;

  pulseCount9 = 0;
  flowRate9 = 0.0;
  flowMilliLitres9 = 0;
  totalMilliLitres9 = 0;
  previousMillis9 = 0;

  pulseCount10 = 0;
  flowRate10 = 0.0;
  flowMilliLitres10 = 0;
  totalMilliLitres10 = 0;
  previousMillis10 = 0;

  attachInterrupt(digitalPinToInterrupt(SENSOR1), pulseCount1er, FALLING);
  attachInterrupt(digitalPinToInterrupt(SENSOR2), pulseCount2er, FALLING);
  attachInterrupt(digitalPinToInterrupt(SENSOR3), pulseCount3er, FALLING);
  attachInterrupt(digitalPinToInterrupt(SENSOR4), pulseCount4er, FALLING);
  attachInterrupt(digitalPinToInterrupt(SENSOR5), pulseCount5er, FALLING);
  attachInterrupt(digitalPinToInterrupt(SENSOR6), pulseCount6er, FALLING);
  attachInterrupt(digitalPinToInterrupt(SENSOR7), pulseCount7er, FALLING);
  attachInterrupt(digitalPinToInterrupt(SENSOR8), pulseCount8er, FALLING);
  attachInterrupt(digitalPinToInterrupt(SENSOR9), pulseCount9er, FALLING);
  attachInterrupt(digitalPinToInterrupt(SENSOR10), pulseCount10er, FALLING);
}

void setupServer()
{

  // Route to load style.css file
  server.on("/style.css", HTTP_GET, [](AsyncWebServerRequest *request)
            { request->send(SPIFFS, "/style.css", "text/css"); });

  // Route to load style.css file
  server.on("/css.css", HTTP_GET, [](AsyncWebServerRequest *request)
            { request->send(SPIFFS, "/css.css", "text/css"); });

  // Route for root / web page
  server.on("/", HTTP_GET, [](AsyncWebServerRequest *request)
            { request->send(SPIFFS, "/index.html"); });
  server.on("/stats", HTTP_GET, [](AsyncWebServerRequest *request)
            {
              buildStatsString();
              request->send_P(200, "text/plain", statsString.c_str());
              statsString = ""; // clear it so it can be built again next time
            });
  server.on("/beer1volume", HTTP_GET, [](AsyncWebServerRequest *request)
            { request->send_P(200, "text/plain", dtostrf(beer1Volume, 6, 2, beer1LitresChar)); });
  server.on("/beer2volume", HTTP_GET, [](AsyncWebServerRequest *request)
            { request->send_P(200, "text/plain", beer2LitresChar); });
  server.on("/beer3volume", HTTP_GET, [](AsyncWebServerRequest *request)
            { request->send_P(200, "text/plain", beer3LitresChar); });
  server.on("/beer4volume", HTTP_GET, [](AsyncWebServerRequest *request)
            { request->send_P(200, "text/plain", beer4LitresChar); });
  server.on("/beer5volume", HTTP_GET, [](AsyncWebServerRequest *request)
            { request->send_P(200, "text/plain", beer5LitresChar); });
  server.on("/beer6volume", HTTP_GET, [](AsyncWebServerRequest *request)
            { request->send_P(200, "text/plain", beer6LitresChar); });
  server.on("/beer7volume", HTTP_GET, [](AsyncWebServerRequest *request)
            { request->send_P(200, "text/plain", beer7LitresChar); });
  server.on("/beer8volume", HTTP_GET, [](AsyncWebServerRequest *request)
            { request->send_P(200, "text/plain", beer8LitresChar); });
  server.on("/beer9volume", HTTP_GET, [](AsyncWebServerRequest *request)
            { request->send_P(200, "text/plain", beer9LitresChar); });
  server.on("/beer10volume", HTTP_GET, [](AsyncWebServerRequest *request)
            { request->send_P(200, "text/plain", beer10LitresChar); });
  server.on("/beer1name", HTTP_GET, [](AsyncWebServerRequest *request)
            {
              request->send_P(200, "text/plain", createNames(beer1Name).c_str());
              Serial.println("/beer1name endpoint hit!");
              beerNameString = "";
            });
  server.on("/beer2name", HTTP_GET, [](AsyncWebServerRequest *request)
            {
              request->send_P(200, "text/plain", createNames(beer2Name).c_str());
              Serial.println("/beer2name endpoint hit!");
              beerNameString = "";
            });
  server.on("/beer3name", HTTP_GET, [](AsyncWebServerRequest *request)
            {
              request->send_P(200, "text/plain", createNames(beer3Name).c_str());
              Serial.println("/beer3name endpoint hit!");
              beerNameString = "";
            });
  server.on("/beer4name", HTTP_GET, [](AsyncWebServerRequest *request)
            {
              request->send_P(200, "text/plain", createNames(beer4Name).c_str());
              Serial.println("/beer4name endpoint hit!");
              beerNameString = "";
            });
  server.on("/beer5name", HTTP_GET, [](AsyncWebServerRequest *request)
            {
              request->send_P(200, "text/plain", createNames(beer5Name).c_str());
              Serial.println("/beer5name endpoint hit!");
              beerNameString = "";
            });
  server.on("/beer6name", HTTP_GET, [](AsyncWebServerRequest *request)
            {
              request->send_P(200, "text/plain", createNames(beer6Name).c_str());
              Serial.println("/beer6name endpoint hit!");
              beerNameString = "";
            });
  server.on("/beer7name", HTTP_GET, [](AsyncWebServerRequest *request)
            {
              request->send_P(200, "text/plain", createNames(beer7Name).c_str());
              Serial.println("/beer7name endpoint hit!");
              beerNameString = "";
            });
  server.on("/beer8name", HTTP_GET, [](AsyncWebServerRequest *request)
            {
              request->send_P(200, "text/plain", createNames(beer8Name).c_str());
              Serial.println("/beer8name endpoint hit!");
              beerNameString = "";
            });
  server.on("/beer9name", HTTP_GET, [](AsyncWebServerRequest *request)
            {
              request->send_P(200, "text/plain", createNames(beer9Name).c_str());
              Serial.println("/beer9name endpoint hit!");
              beerNameString = "";
            });
  server.on("/beer10name", HTTP_GET, [](AsyncWebServerRequest *request)
            {
              request->send_P(200, "text/plain", createNames(beer10Name).c_str());
              Serial.println("/beer10name endpoint hit!");
              beerNameString = "";
            });
  server.on("/allbeernames", HTTP_GET, [](AsyncWebServerRequest *request)
            {
              request->send_P(200, "text/plain", beerNameStringConcatenator().c_str());
              Serial.println("/allbeernames endpoint hit!");
              jsonBeerNamesString = "";
            });
  server.on("/overviewchartname", HTTP_GET, [](AsyncWebServerRequest *request)
            {
              request->send_P(200, "text/plain", createNames(overviewChartName).c_str());
              Serial.println("/overviewchartname endpoint hit!");
              beerNameString = "";
            });

  // Beer naming form
  server.on("/settings", HTTP_GET, [](AsyncWebServerRequest *request)
            { request->send(SPIFFS, "/settings.html"); });

  // Beer consumption over time
  server.on("/consumption", HTTP_GET, [](AsyncWebServerRequest *request)
            { request->send(SPIFFS, "/consumption.html"); });
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
void loop()
{
  timer.run();
  blinkLED();
  readFlows();
  syncVolumes;
  createStats();
  createBeerNames();
  AsyncElegantOTA.loop();
  ws.cleanupClients();
}

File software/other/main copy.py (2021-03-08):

from machine import Pin, I2C, ADC, PWM, deepsleep
from math import floor
from time import sleep
import utime
import sys

import gc
gc.collect()

#import esp
#esp.osdebug(None)  # Turn off vendor O/S debugging messages
#esp.osdebug(0)  # Redirect vendor O/S debugging messages to UART(0)

debug = True

aux1 = Pin(32, Pin.OUT, Pin.PULL_DOWN)  # aux1 battery fet, GPIO32
aux2 = Pin(4, Pin.OUT, Pin.PULL_DOWN)  # aux2 battery fet, GPIO4   

i2c = I2C(scl=Pin(22), sda=Pin(21))

# testing relays
print("Switching off relays")
aux1.off() # turn off BATT 1
aux2.off() # turn off BATT 2

minutes_since_counter_reset = 0 # allows us to reset daily averages

max_battery_voltage = 14.1  # Lead acid, max charge voltage, ~14.1
min_batery_voltage = 11.8   # Lead acid, 0% SOC voltage, ~11.8V
battery_voltage_range = max_battery_voltage - min_batery_voltage

max_aux1_voltage = 0  # Min/Max stats creation
min_aux1_voltage = 15
max_aux2_voltage = 0
min_aux2_voltage = 15

battery_ADC_multiplier = ((105+20)/20)  # (k) battery ADC voltage divider ratio
max_ADC_value = 4095  # 12-bit ADC in the ESP-32
max_ADC_voltage = 3.6  # 3.6V when using ATTN_11DB

aux1_battery = ADC(Pin(34))  # AUX 1 battery voltage
aux1_battery.atten(ADC.ATTN_11DB)  #Full range: 3.3v

aux2_battery = ADC(Pin(35))  # AUX 2 battery voltage
aux2_battery.atten(ADC.ATTN_11DB)  #Full range: 3.3v

aux1 = Pin(32, Pin.OUT, Pin.PULL_DOWN)  # aux1 battery fet, GPIO32
aux2 = Pin(4, Pin.OUT, Pin.PULL_DOWN)  # aux2 battery fet, GPIO4   

sys_ok = Pin(27, Pin.OUT) # system LED

mode_button = Pin(33, Pin.IN, Pin.PULL_UP)

ACS781LLRTR100B = .0132 # 13.2mV/A

# TODO: 
esp32_supply_voltage = 3.28 # Need to actually measure this on the fly
adc_volts_per_devision = esp32_supply_voltage / max_ADC_value

class LM75(object):
    ADDRESS = 0x48  # LM75 bus address
    FREQUENCY = 100000  # I2C bus frequency

    def __init__(self):
        self.i2c = I2C(scl=Pin(22), sda=Pin(21), freq=self.FREQUENCY)

    
    def get_output(self):
        """Return raw output from the LM75 sensor."""
        output = self.i2c.readfrom(self.ADDRESS, 2)
        return output[0], output[1]

    
    def get_temp(self):
        """Return a tuple of (temp_c, point)."""
        temp = self.get_output()
        return int(temp[0]), floor(int(temp[1]) / 23)


def print_temp():
    sensor = LM75()
    temperature, point = sensor.get_temp()
    print("Board temp: %s.%s" % (temperature, point))
    

def adc_value_to_voltage(value):
    return round((max_ADC_voltage/max_ADC_value)*value*battery_ADC_multiplier, 2)
    

def get_ADC_value(pin):
    loop = 0
    adc_value = 0
    while loop < 250:
        loop +=1
        adc_value += pin.read()

    #DEBUG
    #print(adc_value/loop)

    return adc_value_to_voltage(adc_value/loop)
     

def get_aux1_voltage():
    return get_ADC_value(aux1_battery)


def get_aux2_voltage():
    return get_ADC_value(aux2_battery)


def status_led(state):
    if state == 2:
        sys_ok.value(0)
        sleep(1)
        sys_ok.value(not sys_ok.value())
    else:
        sys_ok.value(1)


def aux1_led_flasher(state):
    aux1_led = Pin(25, Pin.OUT)  # Battery 1 LED, GPIO25
    if state == 2:
        aux1_led.value(not aux1_led.value())
    elif state == 1:
        aux1_led.value(1)
    else:
        aux1_led.value(0)


def aux2_led_flasher(state):
    aux2_led = Pin(18, Pin.OUT)  # Battery 2 LED, GPIO18
    if state == 2:
        aux2_led.value(not aux2_led.value())
    elif state == 1:
        aux2_led.value(1)
    else:
        aux2_led.value(0)

def adc_setup():
    i2c.writeto_mem(0x1d, 0x07, b'\x01')
    i2c.writeto_mem(0x1d, 0x00, b'\x01')

def i2c_adc_temp():
    data = i2c.readfrom_mem(0x1d, 0x27, 2)

    high_byte = int(data[0])
    low_byte = int(data[1])

    value = (high_byte << 1 | low_byte >> 7) / 2

    return value

    # every 5 mins: pause everything, disconnect Batt 1 and check its voltage
first_counter = 999
def disconnect_check():
    global first_counter
    modulo_check = int(minutes_since_counter_reset) % 5
    if modulo_check == 0:
        if first_counter == 999:
            print("DISCONNECTING BATT 1 FOR VOLTAGE CHECK")
            aux1.value(0)
            sleep(5)
            aux1_voltage = get_aux1_voltage()
            first_counter = 0
        else:
            aux1_voltage = get_aux1_voltage()
            first_counter = 0
    else:
        aux1_voltage = get_aux1_voltage()
        first_counter = 999


charger_state = None
def charge_state(battery, state):
    global charger_state
    global batt1
    global batt2

    if not batt1 and not batt2:
        charger_state = None

    if charger_state is not None:
        return
    else:
        if battery == 1:
            if state:
                charger_state = "1>2"
        elif battery == 2:
            if state:
                charger_state = "2>1"        

# TODO: add a function to deal with voltage drop due to current draw 
# Can't do this on the lite version as there are now current sensors
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

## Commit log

2021-08-29 Rev 1 - WIP
    [esp32_smart_keezer-B_Cu.gbr, esp32_smart_keezer-B_Mask.gbr, esp32_smart_keezer-B_Paste.gbr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]
2021-09-04 REV 1 - off to JLCPCB
    [esp32_smart_keezer-B_Cu.gbr, esp32_smart_keezer-B_Mask.gbr, esp32_smart_keezer-B_Paste.gbr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]
2021-09-19 WIP - /get broken
    [ESP_Chart_Web_Server.ino]
2021-09-21 Cleaning up
    [esp32_smart_keezer-B_Cu.gbr, esp32_smart_keezer-B_Mask.gbr, esp32_smart_keezer-B_Paste.gbr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]
